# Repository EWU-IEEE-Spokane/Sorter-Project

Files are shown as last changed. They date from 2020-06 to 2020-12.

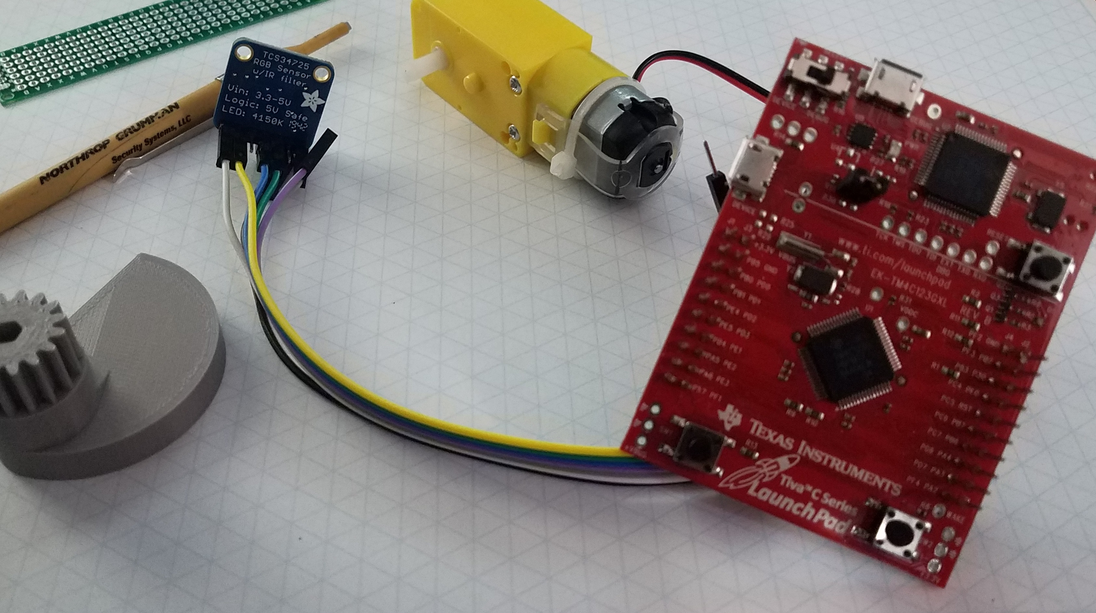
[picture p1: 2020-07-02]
Docs/Mechanical-Engineers/TM4C Color Sensor.jpg

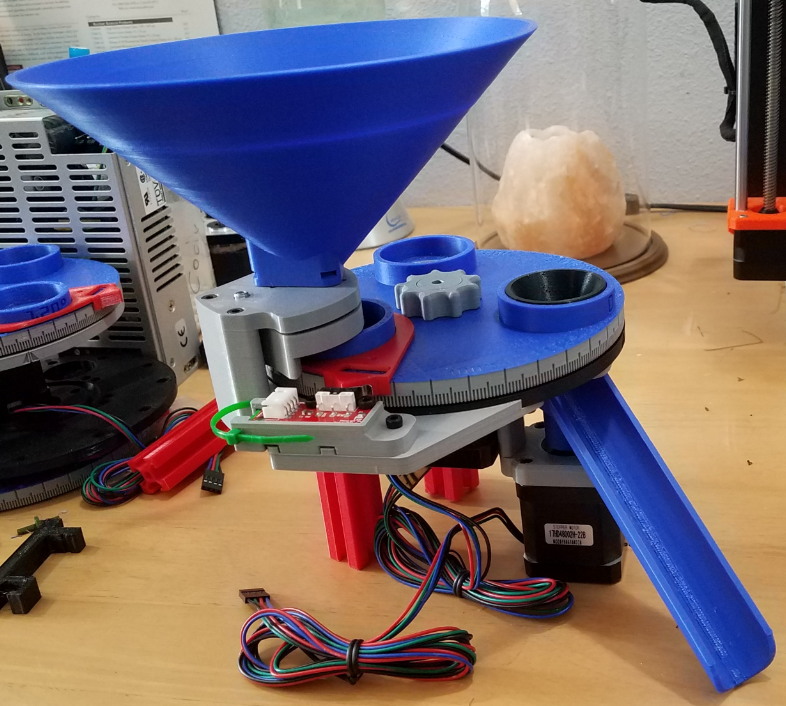
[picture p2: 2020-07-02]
Docs/Mechanical-Engineers/Mechanical Design Printed.PNG

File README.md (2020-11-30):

# Sorter-Project
This is where we host our documentation and code for the Industrial Sorter Project.

# Minutes 11/29/20

We started our meeting looking at the data sheet for the cameras we will be using
    - voti.nl/docs/OV7670.pdf
We also discussed ways to reduce glare in the sorter cups
    - Using a cloth like felt to absorb light
    - Doing the filtering entirely with the image processing algorithm
We talked about ways of getting camera data from the microcontroller to a visible photo
    - Exporting data through UART into a text file, and parsing with some programming language

# Minutes 11/22/20

- We discussed the 3D printed figures from the TinkerCAD fiesta on Friday
    - The printing is going well, other than some more difficult organic shapes

- We discussed methods of holding hand sanitizer
    - Using some kind of sealant on the inside of a 3D printed enclosure
    - Designing parts to screw onto a standard bottle size
    - Using a bag on the inside of the enclosure
    - Partnering with the chemistry department for the solution
    - Solving the problem of viscosity to keep the dispensing speed reasonable
    - Nhat has a working prototype
    - Working on the software side of things

- We revisited the sorter machine design document
    - We accomplished a lot of what we set out to do
    - Some things we descoped, or determined weren't necessary

- We discussed Git and GitHub
    - Over winter break, we may do a workshop
    - Mathew has uploaded his code to GitHub

- We talked about cameras for the image processing
    - Here is a link to the camera we're considering:
        https://www.amazon.com/HiLetgo-OV7670-640x480-0-3Mega-Arduino/dp/B07S66Y3ZQ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

# Minutes 11/8/2020

We started the meeting with discussing a presentable document for the image processing algorithm
- Mathew will be working on this

We had a demo by Cody of the Sorter (sort of) sorting
- There are still some bugs to work out, the machine is moving between extremes

We discussed getting the presentation prepared
- Things to show while talking
- Videos and Documents to discuss
- Start with a video
- Each team creates a slide
- Future developments
- Team organization
- Mechanical design
- PCB design
- Controls software

We set up the sorter project presentation event invitation through IEEE vTools
- Register here! https://events.vtools.ieee.org/m/247537 

# Minutes 10/25/2020

We started our meeting this week with a presentation from Matt on the image processing
- He successfully coded a working algorithm in Matlab
- Next steps are to get some pictures of skittles that will reflect the final output to test the algorithm, and coding the algorithm in C
- We discussed how the camera interfaces with the Tm4C

Cody is working on the final touches for the mechanical design
- Depending on how complex importing 3D models from 360 to Blender will be, Jaidon will make an animation of the sorter

# Minutes 10/18

Mechanical design
    - Cody has had software issues with Fusion 360, so he is considering buying some aluminum extrusion to finish up

User Interface
    - For the user interface, we are aiming for some status lights
        - Idle, run, pause, stop
    - And 3 buttons
        - Start, pause, and E-stop

Parts Distribution
    - Amy has the funds to send parts out if anyone needs any

Pictures for the Easterner
    - We spent a good amount of the meeting taking some in-meeting pictures for the Easterner to use in the story about our club

Member list
    - We came up with an exhaustive list of club members, and estimated class years for each member

# Minutes from 10/4
We came up with a schedule to prepare for the sorter project presentation on November 18th at 5-6pm. The schedule was posted by Cody, here and on Discord.

We talked about a few ideas for the user interface:
- Using a mini industrial control panel
- Creating a PCB for it
- Attaching LEDs to some type of board

We discussed progress of the image processing:
- Possible use of a raspberry pi
- Issues with tm4c interfacing with camera

Upcoming Events:
- a capture the flag event on Tuesday with Gonzaga, time TBD.
- an educational cyber security event mentioned by Stu (talk to Amy for more info.)
- IEEE day on Tuesday October 6th 11-1pm: come see guest speakers, and participate in a competition of ideas.
- Career center meeting Thursday at 2pm
- A visitor from Easterner magazine is coming to talk during the meeting on Wednesday.

Special thanks to John for signing up to IEEE!

# Minutes from 9/27
We discussed the following miscellaneous:
* Image processing projects, and some examples of OCR with Python were shown by yours truly (Jaidon)
* Possibility of changing meeting times: Friday, or later Tuesday?
* Marketing club meetings and IEEE in classes
* Possibility of PLC projects and remote collaboration on code
* Stu possibly talking about cyber security and iot

We talked a bit about parts distribution:
* Parts list surveys
* Prebuilt kits
* Tm4c and basic parts for all

And the following about the sorter specifically:
* PCB progress (completed and functional)
* Cody will try to benchtest this week
* Cody and Nhat will collaborate on agitator
* 3D printing logistics issues (shipping costs, time)
* Jaidon will package PCBs for shipping
* Ian possibly collaborating with Mathew

Below are upcoming club events:
* Soldering tutorial Wednesday at 6
* EWU IEEE story by Easterner magazine in progress
* SAIL meeting Wednesday

We discussed the following possible new projects:
* Weather station
* Music and sound
* Guitar pedals
* Cyber security
* Halloween project
* Lighting driver

Attendance:
* Jaidon
* Chris
* Cody
* Nhat
* Mathew

Ieee members:
* Jaidon
* Chris
* Cody
* Amy
* Nhat
* Michael

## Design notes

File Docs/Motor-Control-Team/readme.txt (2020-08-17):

This folder is where the motor control team can upload their documentation, such as the weekly progress reports.

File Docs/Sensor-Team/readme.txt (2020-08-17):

This folder is where the sensor team can upload their documentation, such as the weekly progress reports.

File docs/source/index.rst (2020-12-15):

.. Sorter-Project documentation master file, created by
   sphinx-quickstart on Mon Dec 14 19:26:34 2020.
   You can adapt this file completely to your liking, but it should at least
   contain the root `toctree` directive.

Welcome to Sorter-Project's documentation!
==========================================

.. toctree::
   :maxdepth: 2
   :caption: Contents:
   
   Intro <intro>
   Mechanical System <mechanical>
   Stepper Motor Control <stepper>
   I2C Communication <i2c>
   Color Sensor <color_sensor>
   Color Processing <color_processing>

Indices and tables
==================

* :ref:`genindex`
* :ref:`modindex`
* :ref:`search`

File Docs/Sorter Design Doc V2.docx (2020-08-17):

EWU IEEE Industrial Sorter Project

Project Goals:

System Design

- Practice designing and documenting a complex system
- Make a modular system that supports division of labor and future changes

Industrial controls

- Implement machine with distributed controls – coincides with remote learning
- Ability to scale controls to PLC, HMI, CAN (TM4C), etc.
- Power control and safety circuits

Motor Control

- Build software drivers and hardware for brushed motors and steppers
- Learn motor theory, power transistors, positional control

Sensors, Image Processing and Communications

- Develop familiarity with I2C protocol (industry standard)
- Manage and interpret sensor data
- Scale towards Machine Vision system (Image processing in R&D stages, camera will also use I2C)
- Image processing may apply Machine Learning in future versions

Microcontrollers/Embedded Systems

- Register-level coding on ARM microcontroller
- Real time operations and fault handling

Teams:

Motor Control Team: Jaidon, Wilson, Nhat

Team Lead: Jaidon

- Motor Control (Steppers) - Jaidon, Wilson

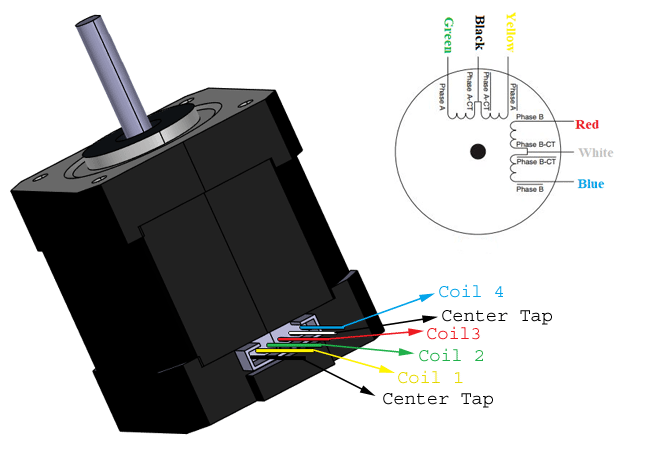
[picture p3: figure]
NEMA 17 Stepper Motor Datasheet, Wiring, Specs & Alternatives

- Agitator Motor – Nhat

Sensor Team: Matt, Amy, Cody, Wilson

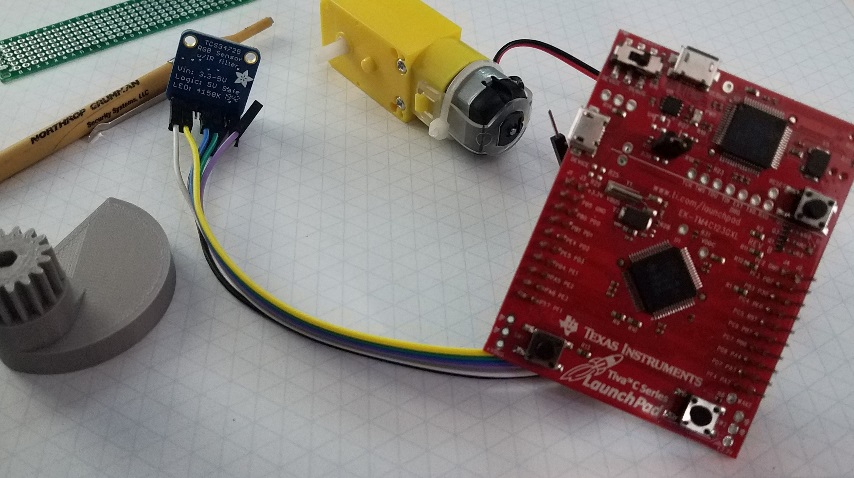
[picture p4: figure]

Team Lead: Cody

- I2C Color Sensor – Amy Swanson, Cody Birkland
- Camera/Image Processing R&D – Matt Sheldon

User Interface Team: Michael, Chris. Nhat

Team Lead:

- LCD R&D Michael
  - 7 segment display for now?

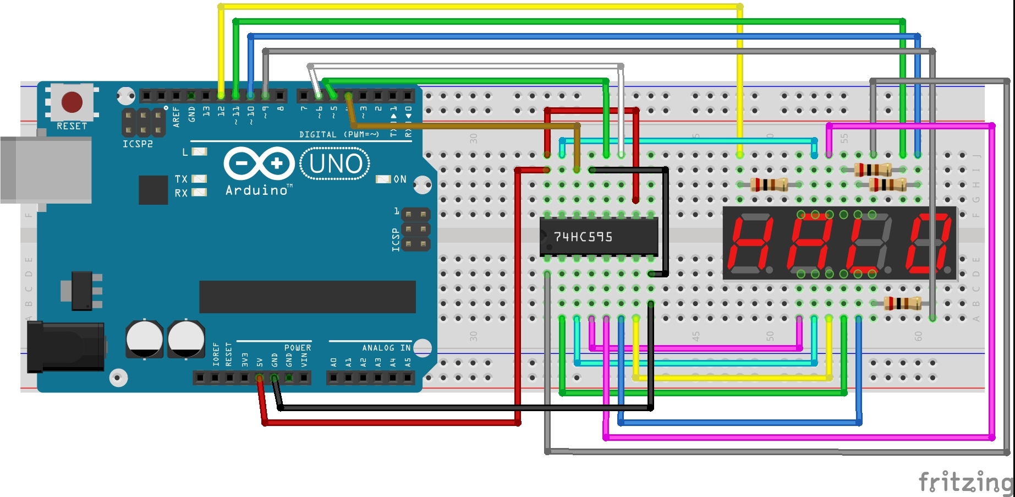
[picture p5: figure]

- Stack Light: Michael

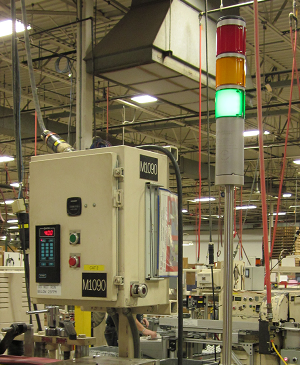
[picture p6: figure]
Stack light - Wikipedia

- Operator Panel – Define switches for control, Define Lights/signals for operation and debug
  - User Interface: Start, Stop (switch), Home (mechanical), E-Stop, Preset (lamp),

Software reset, Debug Mode (switch)

  - Motor Control – “homing” lamp, “ready” lamp
  - Color Sensor – mostly called by software (“sensing color” lamp)
  - Camera calibration when camera is implemented
- RGB LED driver with hex inputs Chris, Michael

System Controls Team: Wilson, Cody

Team Lead: Pending

- Controls Design and Planning
- Mechanical Design – Cody Birkland
- Power System Design (discuss with motor control team)
- Safety Circuits and Controls

Schedule:

Mid-august: Presentable system components

September: Basic working system

~~bench test color sensor to motor interface~~ | | 8/2/2020
Design outline of control systems | | 8/30/2020
finished mechanical prototype | | 8/30/2020
Implement basic user interface | | 9/13/2020
integrate camera and image processing | | 9/27/2020

Next Steps:

- Communicate current system design to user interface team (Cody, Jaidon)
  - Call Diagram
  - Refine Color Sensor code
- Continue mechanical design: chute home switch mount, color sensor mount (Cody)
- Documentation for TM4C programming – setup tutorial (Jaidon: Linux, Amy: Code Composer, Cody/Jaidon: Figure out Visual Studio)
- Prototyping various methods for interfacing: Stack light, UART, 7-segment, etc (User Interface Team)
- Hopper Design and Agitator Motor circuit design (Jaidon and Motor Control Team)
- MISRA C Style Guide PDF £10-20 (Amy talk to Uri) or “ReadTheDocs” designs – discuss in August 4th group meeting
- PLC request from Dr. Walsh (Cody August 3rd)
- Start developing Camera interface (Cody, Matt)

Notes:

Yakindu logic diagram software

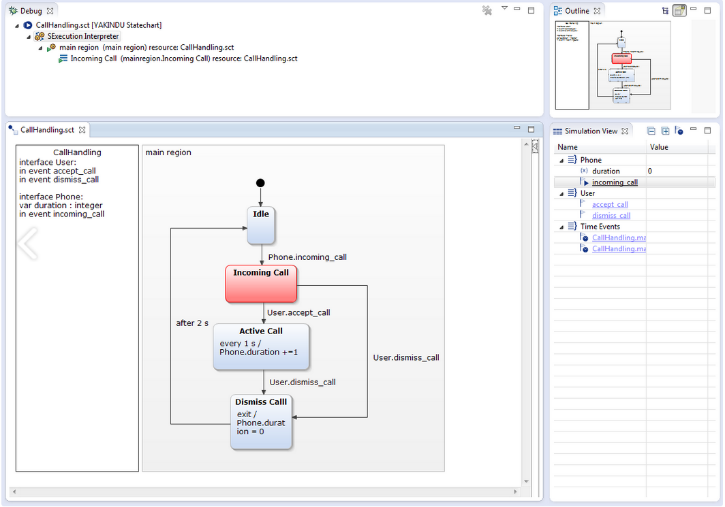
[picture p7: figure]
safety-logic – MoDeS3

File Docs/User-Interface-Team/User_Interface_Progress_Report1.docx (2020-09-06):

Sorter User Interface, Report #1

Goals:

The initial goals for setting up the user interface are to be able to use 4 inputs (Reset, interrupt, Button1, Button2) to move to between 4 simple states that are represented by different LED outputs (Yellow, Red, Green Blue).

What we have done so far:

We have decided on the basic inputs and outputs and how they connect to the user and the LEDs. (See images below)

Worked on getting everyone setup on interfacing with the TM4C.

Gathered all the components we need to prototype the user interface. Put together non-functioning code.

Problems we have had:

Getting everyone setup up to work with the TM4C has been difficult (software to download, compiler errors, etc.).

Limiting the number of inputs to not take up too many pins on the TM4C.

Not knowing what inputs and states we need to implement from other sections of the sorter project.

Actions going forward:

Need to get everybody able to complete the steps necessary to operate the TM4C so we can focus on the fun stuff for the project.

Communicate with the other teams so that we can collaborate more effectively to define the desired inputs, outputs and functionality.

Figure out why the code that we have so far is not operating the way that we would like. Learn how to use the debugger. What is the difference between the device port and the debugger port?

Get all the components connected correctly on the breadboard.

Simple State Diagram

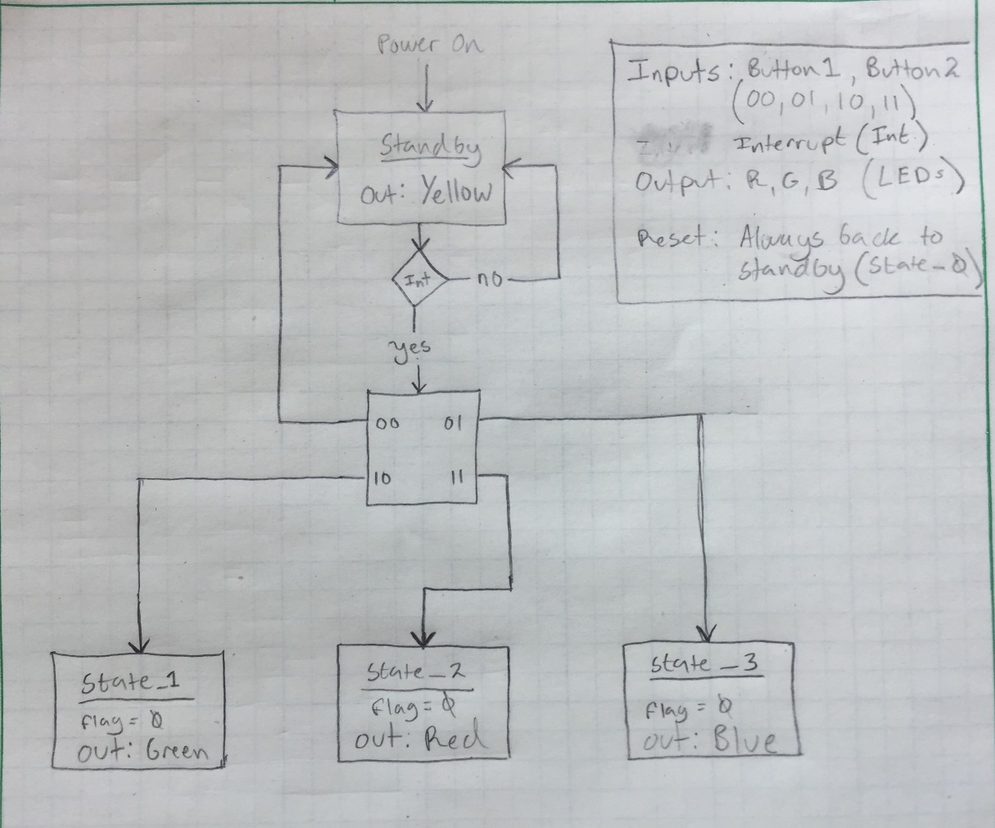
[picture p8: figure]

Input Diagram

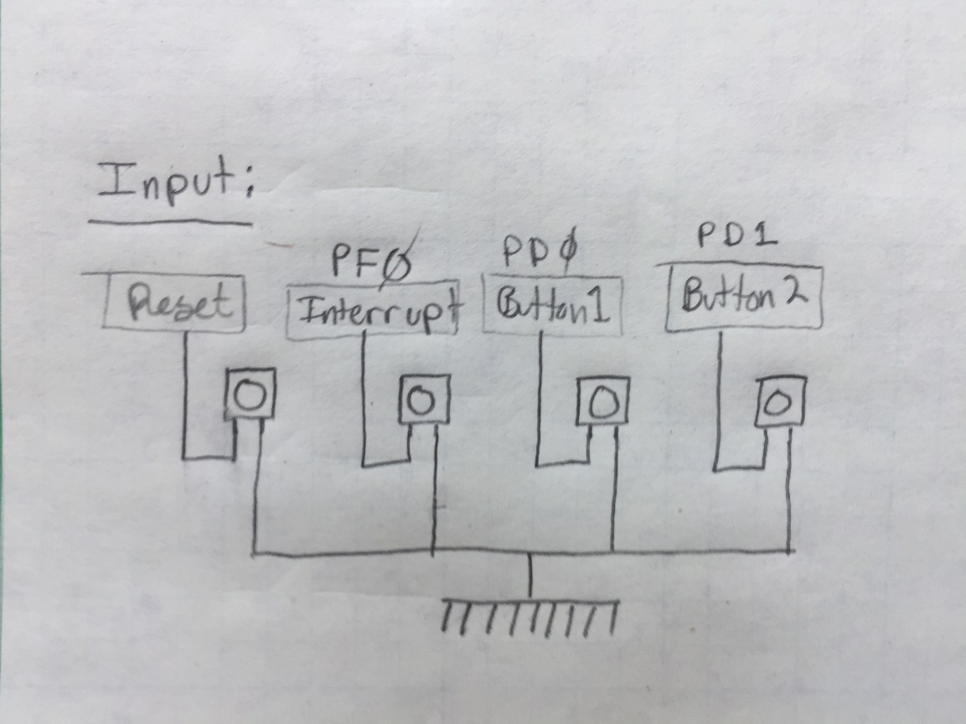
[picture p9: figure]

Output Diagram

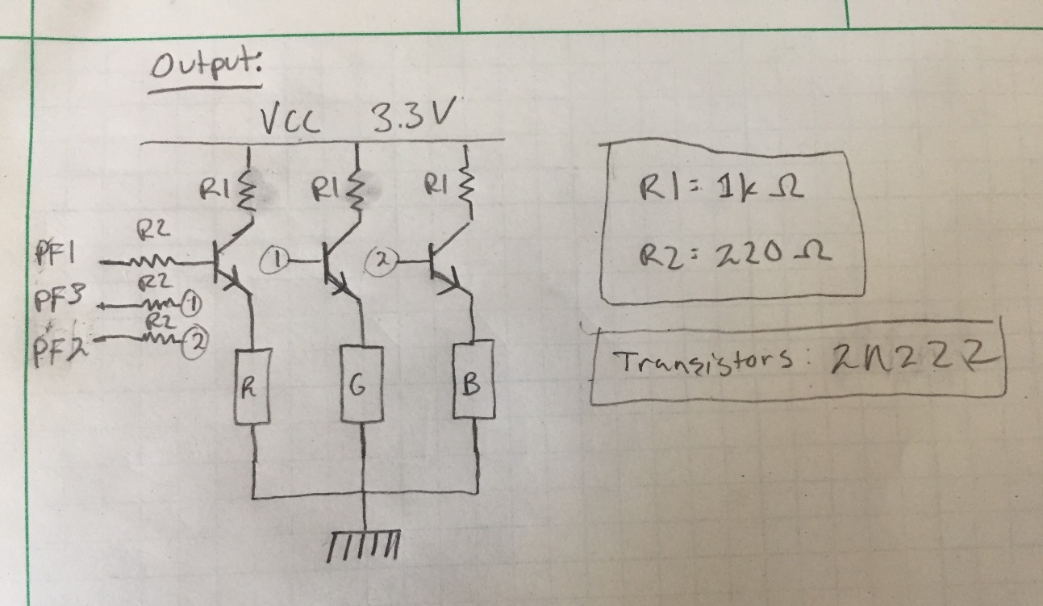
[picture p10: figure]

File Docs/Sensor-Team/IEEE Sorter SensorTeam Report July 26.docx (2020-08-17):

EWU IEEE

Project Weekly Progress Report

Team: Sensors Team

Project: Industrial Sorter

Date: 7/26/2020

What we planned to do last week (copy/paste/summarize previous week)

Last week we planned to continue research into RGB hex color value conversion and gamma correction for the 16-bit color values returned by the color sensor.

We planned a meeting on Saturday in order to catch everyone up on the development of the color sensor code.

Supporting Documentation (website links, GitHub link, pictures)

Basic I2C/Color Sensor Code (initial version that simply obtains 16-bit color values from the sensor): https://github.com/EWU-IEEE-Spokane/TM4C-I2C

UART Output:

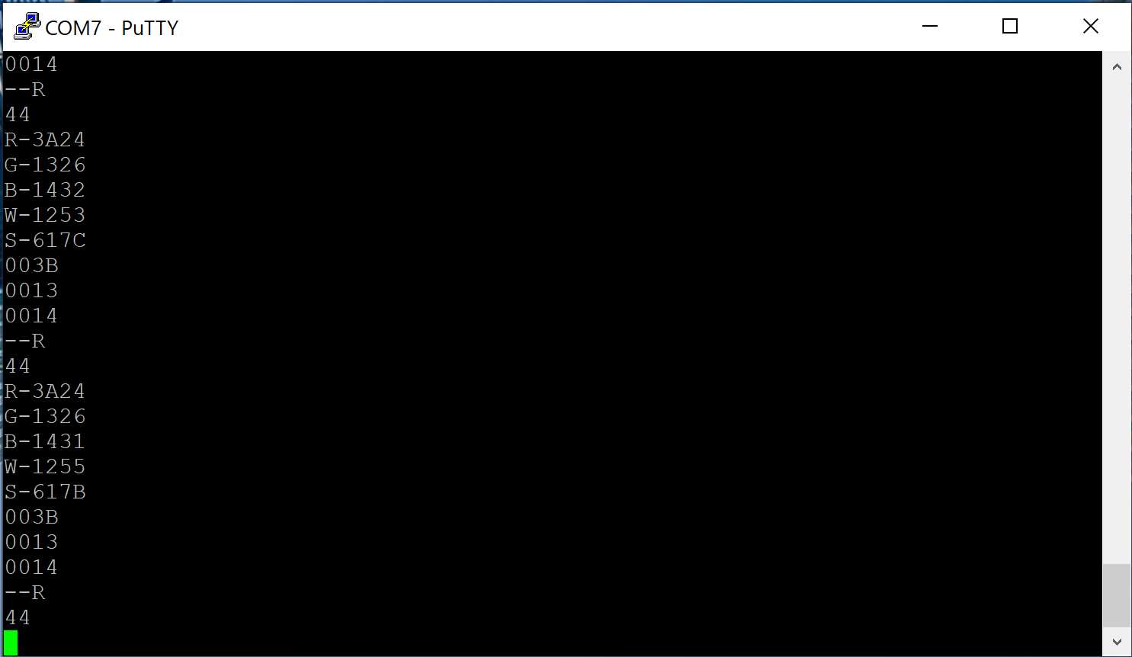
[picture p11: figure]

What we did last week

time spent total: 7 hours

Research:

- Looked into issues with portability of the I2C code. Amy could not compile the code on a Mac, as the compiler had issues on every for loop. Attempted to eliminate initialization within a for loop, but that did not help.

Software:

- Developed sensor code to remove attempts at gamma correction and dynamic compression.
- Added initial attempts to compare color values in their original 16-bit format.

Hardware:

- Built a testing platform for the color sensor that more closely matches the planned end product (enclosed small black tube with colored objects placed at bottom). Before the development work is finalized the CAD models will be developed for the sensor mount and transport cup to enable real-condition testing.

What it accomplished

- We now are ready to develop actual color binning. Being able to sort objects by color will be the majority of the work needed to command the Motor Controller to move based on sorting results.

Why we were unable to accomplish weekly plan if so

- We had to descope in order to make the coming deadline for sensor/motor integration. It is not necessary to implement hex conversion and gamma correction in order to meet this goal. Our time is better spent getting the necessities done.
- We were unable to get the code running on Amy’s machine, so everyone is not caught up on the development. This should be ok as the plan for continued development is linear so it may be best for one person to finish up these items.
- Had issues with compression/gamma correction. Color correction was not working, and results from sensor were definitely digitally saturated (bit overflow). It is possible that analog saturation is causing the sensor to have an incorrect response to color values, where everything is seen as red. Corrections were started by reducing the gain of the sensor from 60x to 4x. Continued analysis is needed.

What we plan to do this week

- Amy will work on parting over the UART code from GitHub in order to gain some insight into why she is having compilation issues. This will also give her a chance to gain familiarity with C for microcontrollers since most of her experience is with assembly language. She’ll also start documenting the setup of Code Composer for the TM4C.
- Cody will develop code that processes the sensor color values into sortation results. The first step will be to resolve the saturation issues so that the sensor returns meaningful values. This may involve tuning of the gain and the integration time of the sensor. It may also be necessary to setup a PWM channel to dim the sensor’s LED.
- Matt will continue camera R&D as time allows, so that there is some refined code ready to be adapted to the camera interface once that is built.
- We need to start communication with the Motion Control Team in order to outline the communication channel between the sensor board and the UMC. We will build a basic interface that drives signals to the motor controller by the end of this week.

How this fits with the overall task/timeline

- We plan to bench test the sensor to motor interface by the end of this week. Getting the sensor to output meaningful color values, then performing a logical sort based on those values will be the majority of what needs to be done on the Sensor Team side of this goal. Adding the motor interface will be more straightforward, though it is dependent on the progress of the Motion Control Team. We will communicate with them in this week’s sorter meeting.
- In order to get meaningful test results from the motor to sensor bench test this week, it may be necessary for the Sensor Team to further descope their design to cut out the incomplete color sorting code. Simply setting up the communication channel and verifying that a list of predetermined sort results can control the motor will give both teams confidence moving forward that they are on the right track. In this case the Sensor Team can add the sorting logic retroactively on top of the tested communication channel.

Why is this important for the project

- Getting this work done will be a major milestone for the project. We will have electronics that will be able to sort objects by color, a communication channel that enables those logical sort results to be passed as control signals to a motor controller, and a motor controller that is able to perform physical sorting.

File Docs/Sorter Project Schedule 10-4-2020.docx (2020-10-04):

Sorter Project Presentation: Wednesday, November 18th at 5-6 PM

Weeks starting Sunday

10-4: Finish Frame design and manufacturing, Agitator mechanical design, Driver design discussion. Continue Image processing

10-11: Full system test with finished mechanical design, implement agitator

10-18: Bug fixes, Cable management, start distributing parts

10-25: Finalize User interface, beautify. Evaluate image processing technology readiness

11-1: Start generating presentation materials (slide show, documentation, video?)

11-8: finish presentation, dress rehearsal

11-15: week of presentation

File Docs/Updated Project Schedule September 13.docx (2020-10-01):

Sorter Project Revised Schedule 9-13-2020

Sept 13 – Attempted complete system prototype initial test:

- Had issues with underpowered 5V power supply (max output 700mA).
- May want to isolate 5V logic rail and 5V motor power
- Need Frame and cable management
- Need to test color sensor performance in actual sorter conditions
- Code had issues with shared global variables for the chute and turntable motors

Sept 20 – Have frame designed, acquire suitable 5V supply, continue user interface design, test improved code, test color sensor performance, start power supply isolation circuit design, test breadboarded prototype

Sept 23 – quarter starts

Sept 27 – Have PCB assembled, attempt another complete system test, start mass producing components, generate BOM and assembly instructions

Oct 4 – have kits shipped out, start integrating user interface

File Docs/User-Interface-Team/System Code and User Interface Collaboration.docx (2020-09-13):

System Code and User Interface Collaboration

EWU IEEE Industrial Sorter Project

September 6, 2020

System code is shown in bold

User interface code wishlist is shown as highlighted

From “Sorter.c”:

Main{

Configure()

ShowReadyLight() //right now the code blinks 3 times to show configure worked

While(presetButtonNotPushed){} //wait until operator hits preset

While(preset){

homeTable()

homeChute()

while(runButtonNotPushed){} //wait here until operator hits start

while(run){

singleSort() //rotate turntable to get product in front of sensor and drop previous into chute

//call sensor code to get sort result integer: 0=reject, 1-5=skittle colors

//move chute to correct cup

if(estop){

preset = FASLE;

run = FALSE;

//break out of loops, but power to motors has been cut so system is safe

}

if(softStop){

run = FALSE;

}

}

}

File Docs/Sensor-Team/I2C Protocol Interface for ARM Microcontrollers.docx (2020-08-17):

I2C Protocol Interface for ARM Microcontrollers

Industrial Sorter Project

Cody Birkland, EWU IEEE Student Chapter

August 16, 2020

Problem:

We need to interface with the color sensor for the first-stage development of the Sorter Project. The TCS34725 Color Sensor uses the I2C protocol for control signals and data, and the TM4C has multiple integrated I2C controllers. We need to understand the details of the protocol such as the signal characteristics, symbol meanings, and other information specific to the color sensor and the microcontroller.

Research:

The details of the I2C Protocol were researched online. The reference used are:

- I2C Basics: https://www.allaboutcircuits.com/technical-articles/introduction-to-the-i2c-bus/
- I2C DigiKey article: https://www.digikey.com/en/articles/why-the-inter-integrated-circuit-bus-makes-connecting-ics-so-easy
- More reading and address list: https://learn.adafruit.com/i2c-addresses
- TCS34725 Datasheet: https://github.com/EWU-IEEE-Spokane/Sorter-Project/blob/master/I2C%20Color%20Sensor/TCS34725%20Datasheet.pdf
- Reference to TM4C Datasheet https://github.com/EWU-IEEE-Spokane/TM4C-Resources/blob/master/TM4C%20Datasheet.pdf - pages:
    - Introduction – Page 997
    - Block diagrams – Page 1008
    - Initialization Procedure – Page 1015
- Info on SCCB (I2C for cameras): http://forums.parallax.com/uploads/attachments/49380/88241.pdf

The protocol is summarized here:

- I2C utilizes a simple 2-wire communication channel consisting of a Serial Clock wire (SCL) and a Serial Data wire (SDA). Both signals are connected to the positive supply voltage via pull up resistors.
- Communications occur between a Master Device which controls the bus and one or more Slave Devices that can send and receive data when commanded to. There are provisions for having Multiple Masters in one bus, but this is not common in basic applications.
- Data is sent one byte (8 bits) at a time in a Transmission Session. A transmission starts with a start signal, then is immediately followed by the 7-bit Address of the Slave Device to be communicated with. This is then followed by a single bit that specifies Read or Write. This determines if the next 8 bits are data Written to the Slave Device, or 8 bits of data Read from the Slave Device. Following the data, the receiving device asserts a single bit Acknowledge (ACK) signal that tells the transmitting device that the data was successfully received. With a valid ACK, the transmitting device can send as many successive bytes of data as necessary, each with their own ACK bit that must be valid. Once the data is sent, the Master Device asserts a Stop signal that terminates the Transmission Session.

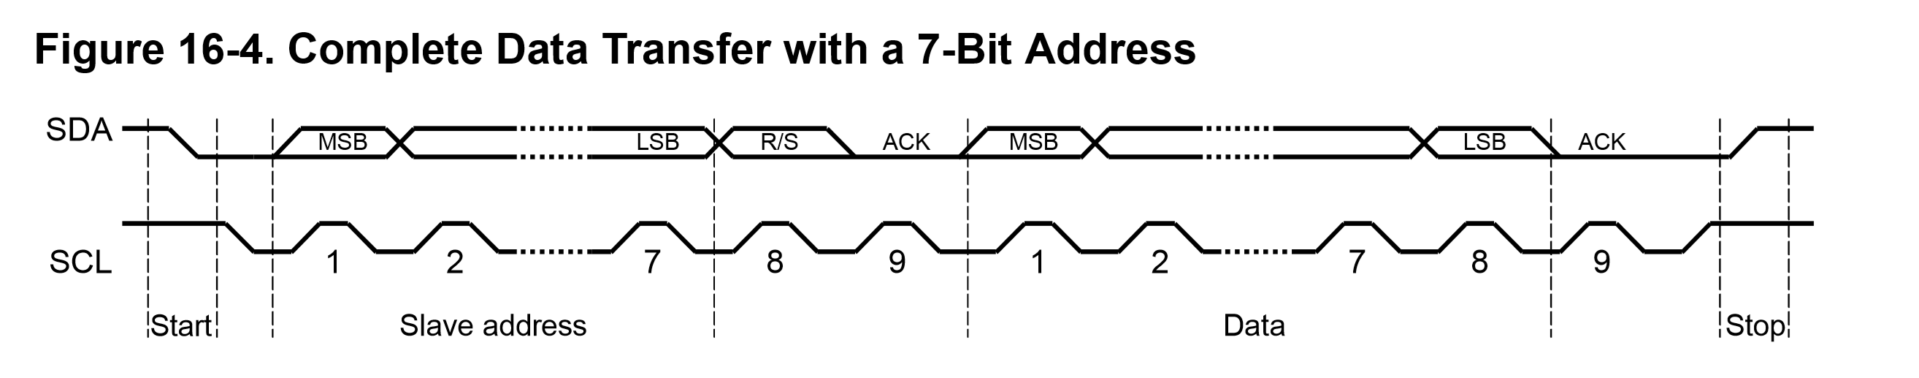
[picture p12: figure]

- Communications can occur in Two modes: A Single Start mode, where an initial Start, Address, and Read/Write command is followed by one or more bytes of data. In this mode, all data in the Transmission is either Read from or Written to the Slave Device. There is also a Repeated Start mode, where multiple Start signals can be used to switch between Read and Write modes without stopping the Transmission.

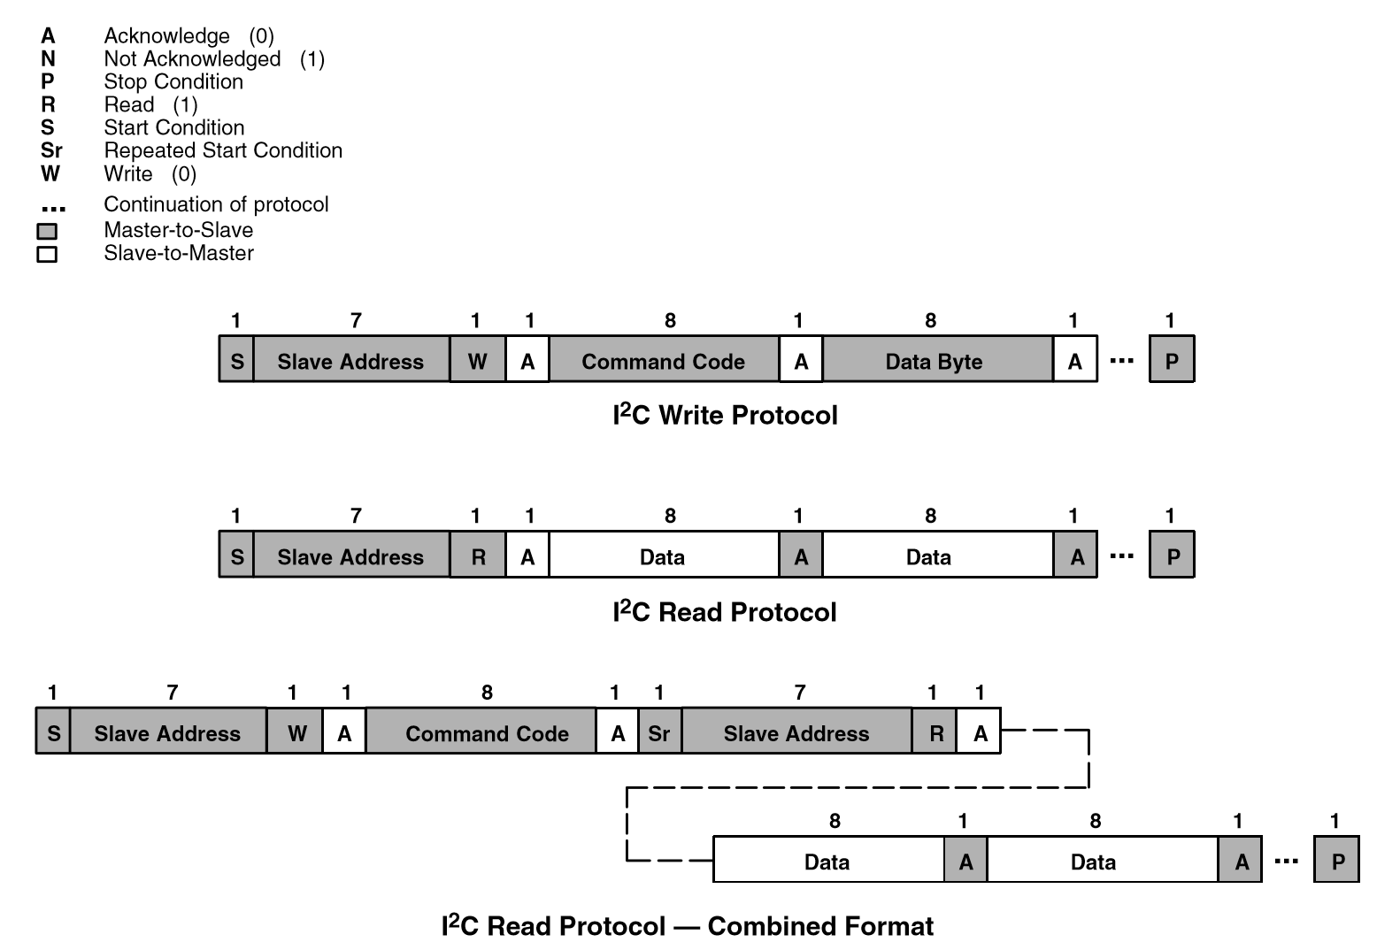
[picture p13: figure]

- There are 4 legal symbols: Start, Data High, Data Low, Stop
- START: Clock high, Data transitions from high to low
- STOP: Clock high, Data transitions from low to high
- Data is either low or high. It is read whenever the clock is high. The data is only permitted to change when the clock is low.
- The ACK signal is the bit immediately following the Data byte, and is low for a successful Acknowledge. This bit behaves the same as a Data bit.

Action:

After learning the intricacies of the protocol, the TM4C Datasheet was used as a guide to develop C code to initialize an I2C module on the Microcontroller then establish a working communication channel with the TCS34725 Color Sensor. After significant debugging, the code was developed to enable reliable communications with the sensor in Single Start mode only.

Initial Code: https://github.com/EWU-IEEE-Spokane/TM4C-I2C

For reasons that have yet to be fully understood, the code implementing a Multiple Start mode driver was not operational and would fail to change the mode of operation. The code also lacks failure handling and an intelligent bus monitoring function. For now, there are significant delays to allow ample time for the communications to complete before moving on. This will need to be optimized in the future.

Value:

Having a working interface for the Color Sensor allows us to move forward with the development of the sensor aspect of the project. This is a vital part of the sorter machine and getting the sensor code working is a major milestone. Additionally, developing an understanding of the I2C protocol will be useful for interfacing with the camera as development continues, since the SCCB protocol that it uses is closely related to I2C.

Beyond this project, the framework for a general-purpose I2C driver for the TM4C will give us a major start towards working with a multitude of different devices. I2C is such a popular communication protocol that there are thousands of devices that use it out there, covering almost everything imaginable such as external memory, accelerometers, and display devices. Before pursuing the many applications out there, we should refine the code to be general purpose, fault tolerant, efficient, and supportive of the Multiple Start mode.

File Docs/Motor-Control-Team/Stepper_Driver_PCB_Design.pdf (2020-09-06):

# Stepper Driver PCB Design

# Skittle Sorter Project Jaidon Lybbert, Motor Control Design Lead, EWU IEEE Student Chapter

08/23/20

This document describes the current stepper motor driver PCB design.

# 3D View:

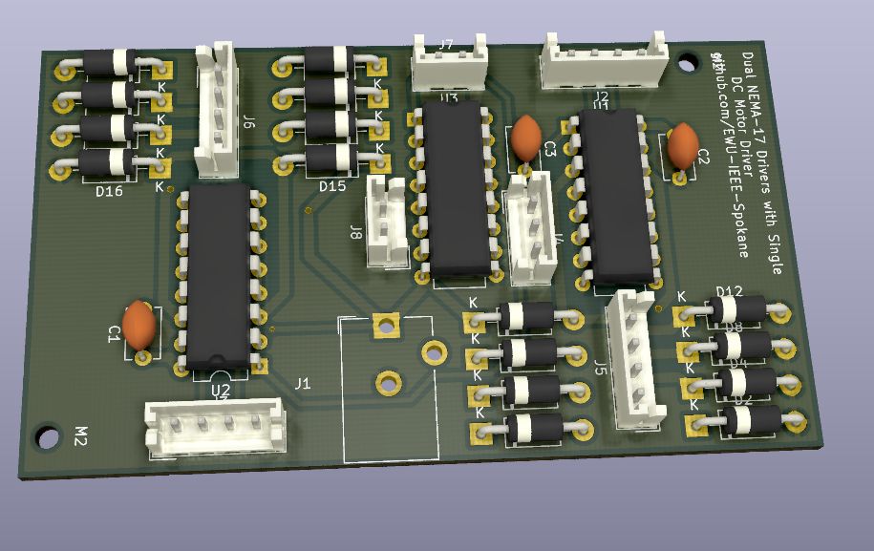
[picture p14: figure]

Fig. 1: Current version of the driver PCB. The outer ICs are l293B chips, and the center IC is an l293D chip. The l293Bs have 2 external 1N4001 flyback diodes for each of their 4 output pins (J5, J6). The connectors at the top end of each IC are the logical inputs (J2, J7, J3) and

# connector J4 has one active high enable pin for each IC. Each IC has one 0.22uF bypass

capacitor for its logic power supply input.

# PCB Specifications: - Layers: 2 - Dimensions: 44.45 x 76.20mm - Thickness: 1.6mm

- Copper weight: 2 Oz.

# Components List:

"Source:" | "C:\Users\Jaidon Lybbert\Documents\Classwork\EENG250\Lab0\MotorDriver\Motor_Driver\Motor_Driver.sch"
"Date:" | "8/23/20 2:54:10 PM"
"Tool:" | "Eeschema (5.1.5-108-gad11b7ebd)-1"
"Component Count:" | "30"
"Ref" | "Value" | "Part" | "Footprint" | "Description" "Vendor"
"C1" | "0.22uF" | "Device:C_Small" | "Capacitor_THT:C_Disc_D5.1mm_W3.2mm_P5.00mm" | "Unpolarized capacitor, small symbol" ""
"C2" | "0.22uF" | "Device:C_Small" | "Capacitor_THT:C_Disc_D5.1mm_W3.2mm_P5.00mm" | "Unpolarized capacitor, small symbol" ""
"C3" | "0.22uF" | "Device:C_Small" | "Capacitor_THT:C_Disc_D5.1mm_W3.2mm_P5.00mm" | "Unpolarized capacitor, small symbol" ""
"D1" | "1N4001" | "Diode:1N4001" | "Diode_THT:D_DO-41_SOD81_P10.16mm_Horizontal" | "50V 1A General Purpose Rectifier Diode, DO-41"
"D2" | "1N4001" | "Diode:1N4001" | "Diode_THT:D_DO-41_SOD81_P10.16mm_Horizontal" | "50V 1A General Purpose Rectifier Diode, DO-41"
"D3" | "1N4001" | "Diode:1N4001" | "Diode_THT:D_DO-41_SOD81_P10.16mm_Horizontal" | "50V 1A General Purpose Rectifier Diode, DO-41"
"D4" | "1N4001" | "Diode:1N4001" | "Diode_THT:D_DO-41_SOD81_P10.16mm_Horizontal" | "50V 1A General Purpose Rectifier Diode, DO-41"
"D5" | "1N4001" | "Diode:1N4001" | "Diode_THT:D_DO-41_SOD81_P10.16mm_Horizontal" | "50V 1A General Purpose Rectifier Diode, DO-41"
"D6" | "1N4001" | "Diode:1N4001" | "Diode_THT:D_DO-41_SOD81_P10.16mm_Horizontal" | "50V 1A General Purpose Rectifier Diode, DO-41"
"D7" | "1N4001" | "Diode:1N4001" | "Diode_THT:D_DO-41_SOD81_P10.16mm_Horizontal" | "50V 1A General Purpose Rectifier Diode, DO-41"
"D8" | "1N4001" | "Diode:1N4001" | "Diode_THT:D_DO-41_SOD81_P10.16mm_Horizontal" | "50V 1A General Purpose Rectifier Diode, DO-41"
"D9" | "1N4001" | "Diode:1N4001" | "Diode_THT:D_DO-41_SOD81_P10.16mm_Horizontal" | "50V 1A General Purpose Rectifier Diode, DO-41"
"D10" | "1N4001" | "Diode:1N4001" | "Diode_THT:D_DO-41_SOD81_P10.16mm_Horizontal" | "50V 1A General Purpose Rectifier Diode, DO-41"
"D11" | "1N4001" | "Diode:1N4001" | "Diode_THT:D_DO-41_SOD81_P10.16mm_Horizontal" | "50V 1A General Purpose Rectifier Diode, DO-41"
"D12" | "1N4001" | "Diode:1N4001" | "Diode_THT:D_DO-41_SOD81_P10.16mm_Horizontal" | "50V 1A General Purpose Rectifier Diode, DO-41"
"D13" | "1N4001" | "Diode:1N4001" | "Diode_THT:D_DO-41_SOD81_P10.16mm_Horizontal" | "50V 1A General Purpose Rectifier Diode, DO-41"
"D14" | "1N4001" | "Diode:1N4001" | "Diode_THT:D_DO-41_SOD81_P10.16mm_Horizontal" | "50V 1A General Purpose Rectifier Diode, DO-41"
"D15" | "1N4001" | "Diode:1N4001" | "Diode_THT:D_DO-41_SOD81_P10.16mm_Horizontal" | "50V 1A General Purpose Rectifier Diode, DO-41"
"D16" | "1N4001" | "Diode:1N4001" | "Diode_THT:D_DO-41_SOD81_P10.16mm_Horizontal" | "50V 1A General Purpose Rectifier Diode, DO-41"
"J1" | "Barrel_Jack""Connector:Barrel_Jack" "Connector_BarrelJack:BarrelJack_Horizontal" | "DC Barrel Jack" | ""
"J2" | "Conn_01x04_Female" | "Connector:Conn_01x04_Female" | "Connector_JST:JST_EH_B4B-EH-A_1x04_P2.50mm_Vertical"
"J3" | "Conn_01x04_Female" | "Connector:Conn_01x04_Female" | "Connector_JST:JST_EH_B4B-EH-A_1x04_P2.50mm_Vertical"
"J4" | "Conn_01x03_Female" | "Connector:Conn_01x03_Female" | "Connector_JST:JST_EH_B3B-EH-A_1x03_P2.50mm_Vertical"
"J5" | "Conn_01x04_Male" | "Connector:Conn_01x04_Male" | "Connector_JST:JST_EH_B4B-EH-A_1x04_P2.50mm_Vertical"
"J6" | "Conn_01x04_Male" | "Connector:Conn_01x04_Male" | "Connector_JST:JST_EH_B4B-EH-A_1x04_P2.50mm_Vertical"
"J7" | "Conn_01x02_Female" | "Connector:Conn_01x02_Female" | "Connector_JST:JST_EH_B2B-EH-A_1x02_P2.50mm_Vertical"
"J8" | "Conn_01x02_Male" | "Connector:Conn_01x02_Male" | "Connector_JST:JST_EH_B2B-EH-A_1x02_P2.50mm_Vertical"
"U1" | "L293B" | "Driver_Motor:L293" | "Package_DIP:DIP-16_W7.62mm" | "Quadruple Half-H Drivers"""
"U2" | "L293B" | "Driver_Motor:L293" | "Package_DIP:DIP-16_W7.62mm" | "Quadruple Half-H Drivers"""
"U3" | "L293D" | "Driver_Motor:L293D" | "Package_DIP:DIP-16_W7.62mm" | "Quadruple Half-H Drivers"""

# Additional notes: - The l293B chips require heatsinks

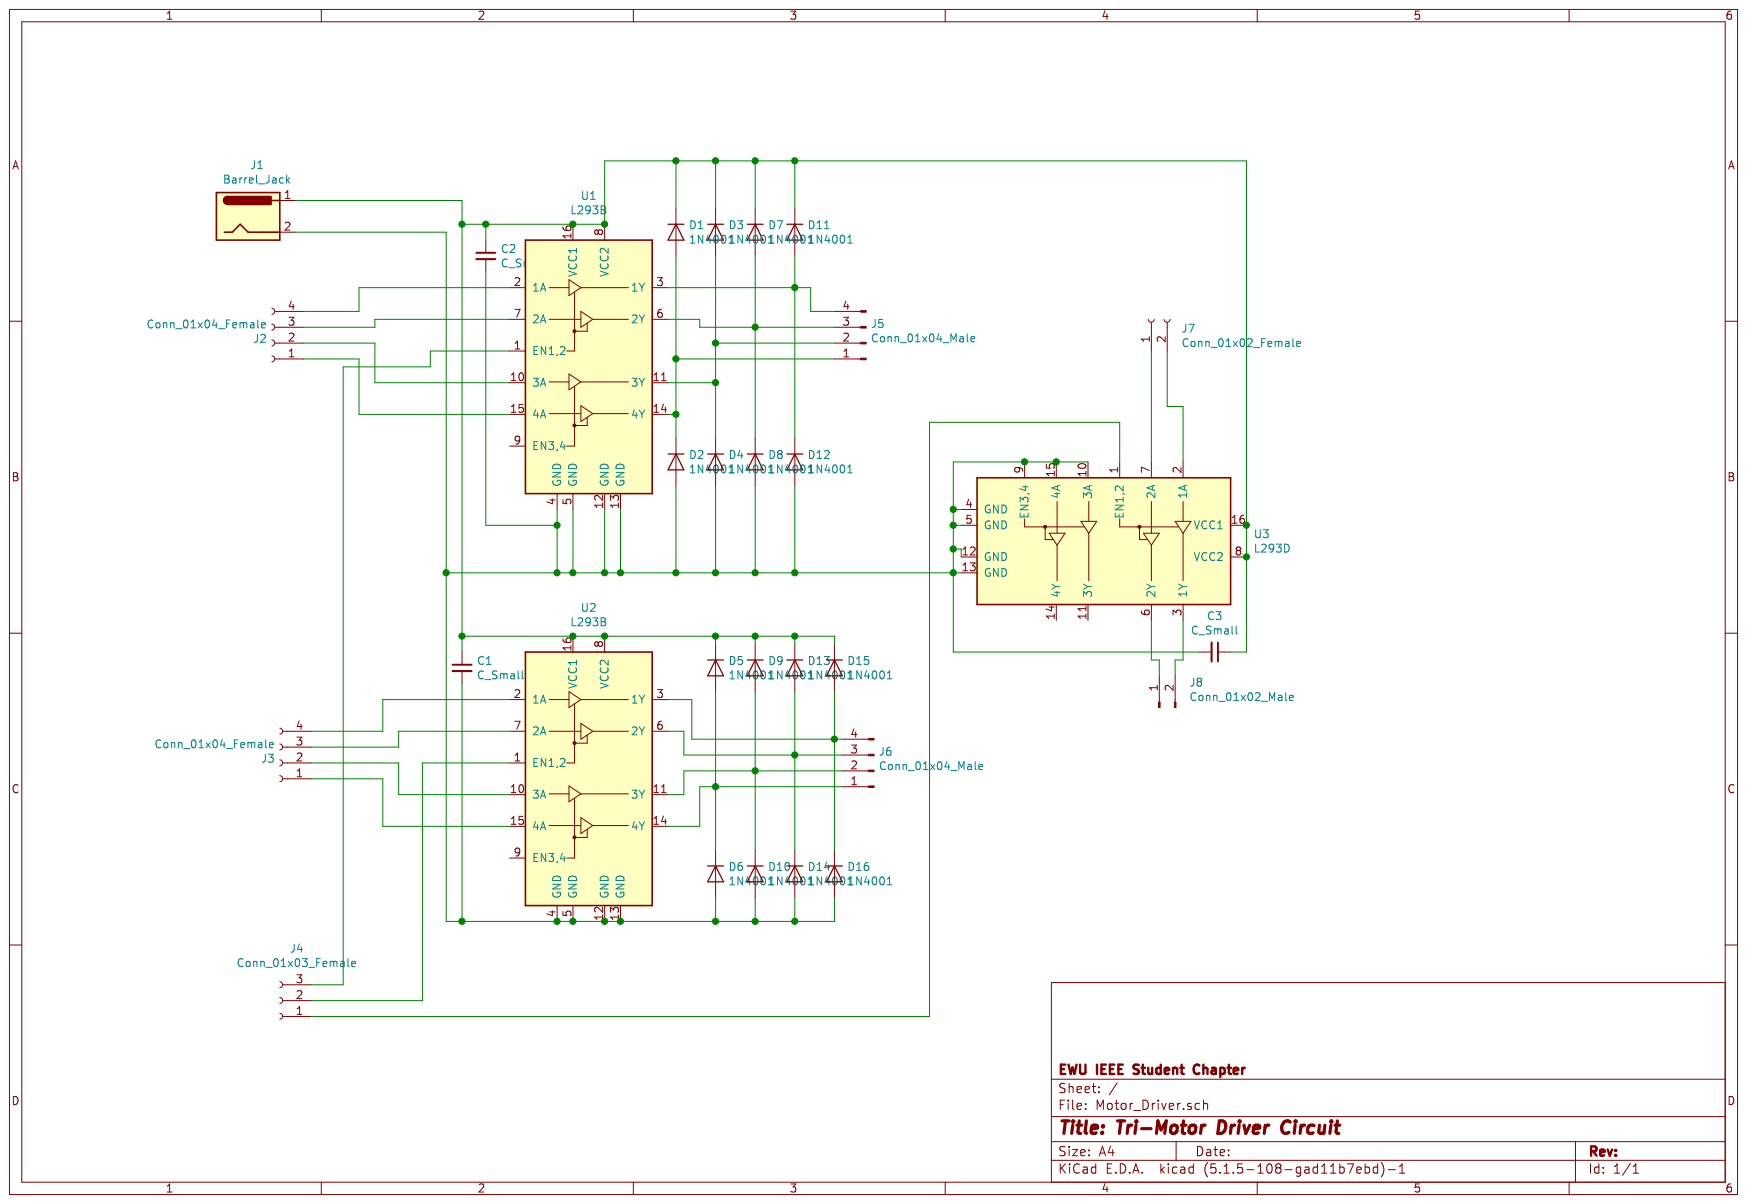
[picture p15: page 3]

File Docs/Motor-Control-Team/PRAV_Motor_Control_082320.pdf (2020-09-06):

### Motor Control Progress Report #8

Skittle Sorter Project
Jaidon Lybbert, Motor Control Design Lead, EWU IEEE Student Chapter
Week of 08/23/20

Problem:
- The PCB design for the motor driver circuit was missing current limiting resistors on the l293B outputs
- A team member (Wilson) was interested in the motor control development, but needed assistance catching up to the current state of the project

Research:
- A 2W 2 Ohm resistor was found, and the dimensions were used to choose the correct footprints

Action:
- The PCB design was modified to accommodate the new components
- A meeting was made with Wilson, in which we were able to get his sorter prototype working with the latest code

Value:
- With the new additions, the PCB design is ready to be sent off for manufacturing
- Bringing additional team members up to date will allow for concurrent development

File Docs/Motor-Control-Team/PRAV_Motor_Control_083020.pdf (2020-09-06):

### Motor Control Progress Report #9

Skittle Sorter Project
Jaidon Lybbert, Motor Control Design Lead, EWU IEEE Student Chapter Week of 08/30/20

Problem:
- The completed PCB design had not been reviewed and sent off for manufacturing
- No progress with implementing ReadTheDocs had been made
- System timing uses busy wait loops and is not tied to any real time
- Wilson needed additional help getting caught up with code development

Research:
- Usage of the SysTick peripheral on the tm4c from the datasheet
- Implementation of ReadTheDocs with github
- https://docs.readthedocs.io/en/stable/intro/getting-started-with-sphinx.html
- Sphinx
- https://docs.readthedocs.io/en/stable/intro/getting-started-with-sphinx.html
- https://www.sphinx-doc.org/en/master/
- reStructuredText
- https://www.sphinx-doc.org/en/master/usage/restructuredtext/basics.html

Action:
- Sent PCB design to JCLPCB for manufacturing
- Implemented ReadTheDocs for a private repository as practice
- Modified sorter.c and stepper.c functions to use real times, by adopting existing code written by Amy Swanson
- A meeting was made with Wilson, in which we went over the stepper code implementation, and he was able to build the project with make

Value:
- Everything is done with the PCBs until they get delivered
- ReadTheDocs will allow us to create user friendly documentation of our code
- System timing is now predictable and precise

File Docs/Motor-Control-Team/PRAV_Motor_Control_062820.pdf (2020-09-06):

### Motor Control Progress Report #2

Skittle Sorter Project
Jaidon Lybbert, Motor Control Design Lead, EWU IEEE Student Chapter
Week of 06/28/20

Problem:
- With the limitations of being a remote organization, and much of our work being done in software, we need a way to collaborate effectively and in an organized manner
- With separate teams working on different systems, it is necessary to communicate our designs to one another to fit them together and avoid conflicts

Research:
- While organizing my section of the newly formed GitHub page, I researched the formatting of a .gitignore file to exclude object files and other unnecessary files from being pushed to the repository and cluttering the filesystem.
- https://git-scm.com/docs/gitignore

Action:
- Created a design document for the universal motor controller (UMC) including inputs and outputs to act as a reference material for myself and other teams
- Created a development document to communicate my progress
- Uploaded current code to GitHub, and organized folders
- The following commits were made:
- Created design document for UMC
- Uploaded project code to GitHub
- Added development document
- Organized and configured .gitignore

Value:
- Using team-oriented development tools encourages others to do the same, and fosters consistent progress and activity within the organization
- Creating design documentation allows others to interface with your section of the project easily
- Communicating progress, and maintaining a history, lowers the barrier of entry for newcomers to the team

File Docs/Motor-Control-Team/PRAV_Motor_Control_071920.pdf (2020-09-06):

### Motor Control Progress Report #3

Skittle Sorter Project
Jaidon Lybbert, Motor Control Design Lead, EWU IEEE Student Chapter
Week of 07/19/20

Problem:
- As code grows, it is necessary to make adjustments to the structure to make it more maintainable, in this case, my code had outgrown its single stepper.c file, and needed to be split into sections that made sense and were portable
- Development thus far had been using a unipolar 4-phase 28byj-48 stepper motor, which is not the motor used for our project, small modifications to the code had to be made to adapt to the bipolar 2-phase NEMA-17 motor
- The NEMA-17 motor requires a large current, and a beefier driver circuit, for this we decided on the l293B dual H-bridge driver, which would need to be interfaced with the motor

Research:
- Splitting files required some brush up on how to link compiled c object files using make, as well as what should and should not be included in a header file
- https://www.cs.colby.edu/maxwell/courses/tutorials/maketutor/
- https://www.tutorialspoint.com/cprogramming/c_header_files.htm
- Learning about how a bipolar stepper motor is driven compared to a unipolar motor was a necessity. The following document contains very detailed information about different methods of driving stepper motors
- https://www.st.com/resource/en/application_note/cd00003774-stepper-motor-drivi ng-stmicroelectronics.pdf (https://www.st.com/resource/en/application_note/cd00003774-stepper-motor-driving-stmicroelectronics.pdf)
- It was necessary to refer to the L293B datasheet to interface the IC with the motor
- https://www.st.com/resource/en/datasheet/l293b.pdf
- Flyback diodes were used in the driver circuit, and consequently researched
- https://en.wikipedia.org/wiki/Flyback_diode

Action:
- The huge stepper.c file was split into init.c, umc.c, and stepper.c, with associated header files
- The code was modified to add support for driving the NEMA-17 motor
- A “home” switch input was added to an onboard button along with an associated debouncing function
- The driver circuit was built, and interfaced with the tm4c and NEMA-17 for testing

Value:
- Maintaining existing code improves readability and prevents future issues from arising
- Constructing the circuit for the NEMA-17 allows for testing of the software and hardware, as well as further development of functionality
- Basic inputs to the system allows for more robust testing

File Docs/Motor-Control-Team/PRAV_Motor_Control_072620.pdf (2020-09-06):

### Motor Control Progress Report #4

Skittle Sorter Project
Jaidon Lybbert, Motor Control Design Lead, EWU IEEE Student Chapter
Week of 07/26/20

Problem:
- Until now, most of the inputs for testing have been done in software. In order to interface to the rest of the system, hardware inputs must be used
- Through the development process, certain code blocks and parameters to functions have become obsolete
- The motor had not been tested with the color sensor, which is another module with significant progress made, and which functions on its own
- While we originally intended to have the motor control implemented on a separate microcontroller than the rest of the components in the system, it was determined that it would be more reasonable to implement many of the systems on the same board along with the motor controller

Research:
- The I2C protocol was researched for some background knowledge in order to understand the color sensor’s code
- https://learn.sparkfun.com/tutorials/i2c/all

Action:
- Inputs were initialized for the UMC according to the design document
- Unnecessary parameters were removed from code functions
- A central control file “sorter.c” was added to call functions from both motor control and sensor code
- A meeting was made with the sensor team, and the motor control was successfully integrated with the color sensor. We were able to read a color, and the chute correctly moved to the corresponding color’s bin location.
- It was decided that the motor controller would have software inputs as opposed to hardware inputs in order to make the interfacing process easier to implement and maintain, as well as save on components

Value:
- A central control file allows us to keep existing, working code separate from new, rapidly developing code
- Interfacing the two systems opened our eyes to the error in our design approaches, and allowed us to make adjustments accordingly
- Now that the two systems are interfaced and work, we are much closer to a presentable working product

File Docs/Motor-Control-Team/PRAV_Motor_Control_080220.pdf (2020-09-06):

### Motor Control Progress Report #5

Skittle Sorter Project
Jaidon Lybbert, Motor Control Design Lead, EWU IEEE Student Chapter
Week of 08/02/20

Problem:
- Because we decided we are going to interface with the stepper motor control through software rather than hardware, the code has to be modified to take controls as parameters in code, rather than as GPIO inputs. Additionally, since the UMC was intended to be dedicated to a single motor, the code now must be abstracted so that it can be used for several motors.
- The I2C.c code used for the color sensor was large and consisted of several sections (I2C, UART, color processing) that could be separated into individual modules.
- The motor control code had dependencies that were implementation specific (init.c primarily) which prevented the code from being separated and used elsewhere
- The color sensor and motor control worked together, but had bugs
- Issues arose using VSCode to flash binaries to the tm4c when the current flashed program included the color sensor code

Research:
- Research was done on color sensor used in order to integrate the hardware into my home project setup, and further understand the sensor code
- https://www.alldatasheet.com/view_datasheet.jsp?Searchword=TCS34725

Action:
- Abstracted stepper code to be functional with multiple motors driven from the same tm4c
- Helped color sensor team in splitting large I2C.c file into smaller modules
- Removed dependencies and hardcoded addresses from stepper code
- Fixed bugs with integration of the sensor code with the motor driving code

Value:
- With the new code abstractions, we will be able to drive stepper motors for both the chute and the table components of the sorting machine
- By splitting the I2C.c file, we are now able to port the smaller modules into other projects in the future, without including a lot of unnecessary code that would add clutter and confusion
- Removing dependencies and hardcoded addresses from the stepper code prepares us to eventually compile this code as a library object file to be used in projects without the need for recompiling
- Fixing the bugs introduced with the interface of the two systems allows for further testing and integration with the remaining systems

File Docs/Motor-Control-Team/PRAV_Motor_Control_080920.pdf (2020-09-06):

### Motor Control Progress Report #6

Skittle Sorter Project
Jaidon Lybbert, Motor Control Design Lead, EWU IEEE Student Chapter
Week of 08/09/20

Problem:
- Little control structure was in place for running the system. As a result, the system would run its test sequence the moment the code was flashed, with no start or stop inputs.
- Although the code was updated to facilitate adding a second motor, no code was in place to implement a second motor.
- The control code (sorter.c) lacked any substantive comments.
- The user interface team was in need of an accessible way to understand the motor control code to make use of its functions.
- The sequence that occurs when executing an interrupt was not understood

Research:
- Setting up interrupts on the tm4c
- http://users.ece.utexas.edu/~valvano/Volume1/E-Book/C12_Interrupts.htm
- Context switching, kernels
- https://dmitryfrank.com/articles/how_i_ended_up_writing_my_own_kernel
- https://en.wikipedia.org/wiki/Kernel_(operating_system)
- RISC
- https://en.wikipedia.org/wiki/Reduced_instruction_set_computer
- SoCs
- https://en.wikipedia.org/wiki/System_on_a_chip
- https://electronics.stackexchange.com/questions/16828/microcontroller-vs-syste m-on-chip (https://electronics.stackexchange.com/questions/16828/microcontroller-vs-system-on-chip)
- Assembly language
- https://www.tutorialspoint.com/assembly_programming/assembly_basic_syntax.h tm (https://www.tutorialspoint.com/assembly_programming/assembly_basic_syntax.htm)
- Linker scripts
- https://wiki.osdev.org/Linker_Scripts

Action:
- Added start input to the testing sequence, and different modes of testing for separate hardware configurations
- Initialized ports and defines for second motor output
- Added descriptive comments throughout the control/testing code
- Drew up function call diagrams for relevant functions in the stepper code

Value:
- The motor control code is now considered functionally complete, and ready to be integrated with the rest of the system as they are completed
- Through comments and documentation, interfacing with the motor control code has been made easier for other teams
- A better understanding of interrupt execution, lower levels of programming, and the linking process may help to avoid bugs in the future

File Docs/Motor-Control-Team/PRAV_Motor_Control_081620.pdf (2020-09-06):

### Motor Control Progress Report #7

Skittle Sorter Project
Jaidon Lybbert, Motor Control Design Lead, EWU IEEE Student Chapter
Week of 08/16/20

Problem:
- The motor driver circuit using the l293b has been prototyped on a breadboard, which is a temporary solution, and has poor cooling, causing the chip to melt the breadboard when run for extended periods of time
- Motor control development has been done on a separate branch on GitHub for several weeks, and merge conflicts have shown up between the motor control branch and the master branch
- Motor control progress reports have been in scattered formats and memos without a defined format

Research:
- Resolving merge conflicts on GitHub
- https://docs.github.com/en/github/collaborating-with-issues-and-pull-requests/res olving-a-merge-conflict-using-the-command-line (https://docs.github.com/en/github/collaborating-with-issues-and-pull-requests/resolving-a-merge-conflict-using-the-command-line)
- Using KiCad to design PCBs
- See “Getting Started with KiCad” at the end of this report

Action:
- Researched PCB design and manufacturing
- Learned KiCad
- Designed and redesigned PCB for the driver circuit
- See “Stepper Driver PCB Design” and “Stepper Driver PCB Iterations” at the end of this report
- Merged the motor control branch to the master branch on GitHub
- Consolidated weeks of notes into polished progress reports

Value:
- Merging multiple weeks of changes onto the master branch finalizes the changes and brings our main development branch up to date
- A PCB for the driver circuit will allow us to clean up our hardware to make it more presentable, easier to use, and allows for better cooling of the ICs
- Knowledge of designing PCBs will aid in future projects that require them
- A clear history of progress with the motor control will help new team members get up to date, as well as communicate new changes with other teams

### Stepper Driver PCB Design

Jaidon Lybbert, Motor Control Design Lead, EWU IEEE Student Chapter 08/23/20

This document describes the current stepper motor driver PCB design.

3D View:


Fig. 1: Current version of the driver PCB. The outer ICs are l293B chips, and the center IC is an l293D chip. The l293Bs have 2 external 1N4001 flyback diodes for each of their 4 output pins (J5, J6). The connectors at the top end of each IC are the logical inputs (J2, J7, J3) and connector J4 has one active high enable pin for each IC. Each IC has one 0.22uF bypass capacitor for its logic power supply input.

PCB Specifications:
- Layers: 2
- Dimensions: 44.45 x 76.20mm
- Thickness: 1.6mm
- Copper weight: 2 Oz.

Components List:

"Source:" | "C:\Users\Jaidon Lybbert\Documents\Classwork\EENG250\Lab0\MotorDriver\Motor_Driver\Motor_Driver.sch"
"Date:" | "8/23/20 2:54:10 PM"
"Tool:" | "Eeschema (5.1.5-108-gad11b7ebd)-1"
"Component Count:" | "30"
"Ref" | "Value" | "Part" | "Footprint" | "Description" "Vendor"
"C1" | "0.22uF" | "Device:C_Small" | "Capacitor_THT:C_Disc_D5.1mm_W3.2mm_P5.00mm" | "Unpolarized capacitor, small symbol" ""
"C2" | "0.22uF" | "Device:C_Small" | "Capacitor_THT:C_Disc_D5.1mm_W3.2mm_P5.00mm" | "Unpolarized capacitor, small symbol" ""
"C3" | "0.22uF" | "Device:C_Small" | "Capacitor_THT:C_Disc_D5.1mm_W3.2mm_P5.00mm" | "Unpolarized capacitor, small symbol" ""
"D1" | "1N4001" | "Diode:1N4001" | "Diode_THT:D_DO-41_SOD81_P10.16mm_Horizontal" | "50V 1A General Purpose Rectifier Diode, DO-41"
"D2" | "1N4001" | "Diode:1N4001" | "Diode_THT:D_DO-41_SOD81_P10.16mm_Horizontal" | "50V 1A General Purpose Rectifier Diode, DO-41"
"D3" | "1N4001" | "Diode:1N4001" | "Diode_THT:D_DO-41_SOD81_P10.16mm_Horizontal" | "50V 1A General Purpose Rectifier Diode, DO-41"
"D4" | "1N4001" | "Diode:1N4001" | "Diode_THT:D_DO-41_SOD81_P10.16mm_Horizontal" | "50V 1A General Purpose Rectifier Diode, DO-41"
"D5" | "1N4001" | "Diode:1N4001" | "Diode_THT:D_DO-41_SOD81_P10.16mm_Horizontal" | "50V 1A General Purpose Rectifier Diode, DO-41"
"D6" | "1N4001" | "Diode:1N4001" | "Diode_THT:D_DO-41_SOD81_P10.16mm_Horizontal" | "50V 1A General Purpose Rectifier Diode, DO-41"
"D7" | "1N4001" | "Diode:1N4001" | "Diode_THT:D_DO-41_SOD81_P10.16mm_Horizontal" | "50V 1A General Purpose Rectifier Diode, DO-41"
"D8" | "1N4001" | "Diode:1N4001" | "Diode_THT:D_DO-41_SOD81_P10.16mm_Horizontal" | "50V 1A General Purpose Rectifier Diode, DO-41"
"D9" | "1N4001" | "Diode:1N4001" | "Diode_THT:D_DO-41_SOD81_P10.16mm_Horizontal" | "50V 1A General Purpose Rectifier Diode, DO-41"
"D10" | "1N4001" | "Diode:1N4001" | "Diode_THT:D_DO-41_SOD81_P10.16mm_Horizontal" | "50V 1A General Purpose Rectifier Diode, DO-41"
"D11" | "1N4001" | "Diode:1N4001" | "Diode_THT:D_DO-41_SOD81_P10.16mm_Horizontal" | "50V 1A General Purpose Rectifier Diode, DO-41"
"D12" | "1N4001" | "Diode:1N4001" | "Diode_THT:D_DO-41_SOD81_P10.16mm_Horizontal" | "50V 1A General Purpose Rectifier Diode, DO-41"
"D13" | "1N4001" | "Diode:1N4001" | "Diode_THT:D_DO-41_SOD81_P10.16mm_Horizontal" | "50V 1A General Purpose Rectifier Diode, DO-41"
"D14" | "1N4001" | "Diode:1N4001" | "Diode_THT:D_DO-41_SOD81_P10.16mm_Horizontal" | "50V 1A General Purpose Rectifier Diode, DO-41"
"D15" | "1N4001" | "Diode:1N4001" | "Diode_THT:D_DO-41_SOD81_P10.16mm_Horizontal" | "50V 1A General Purpose Rectifier Diode, DO-41"
"D16" | "1N4001" | "Diode:1N4001" | "Diode_THT:D_DO-41_SOD81_P10.16mm_Horizontal" | "50V 1A General Purpose Rectifier Diode, DO-41"
"J1" | "Barrel_Jack""Connector:Barrel_Jack" "Connector_BarrelJack:BarrelJack_Horizontal" | "DC Barrel Jack" | ""
"J2" | "Conn_01x04_Female" | "Connector:Conn_01x04_Female" | "Connector_JST:JST_EH_B4B-EH-A_1x04_P2.50mm_Vertical"
"J3" | "Conn_01x04_Female" | "Connector:Conn_01x04_Female" | "Connector_JST:JST_EH_B4B-EH-A_1x04_P2.50mm_Vertical"
"J4" | "Conn_01x03_Female" | "Connector:Conn_01x03_Female" | "Connector_JST:JST_EH_B3B-EH-A_1x03_P2.50mm_Vertical"
"J5" | "Conn_01x04_Male" | "Connector:Conn_01x04_Male" | "Connector_JST:JST_EH_B4B-EH-A_1x04_P2.50mm_Vertical"
"J6" | "Conn_01x04_Male" | "Connector:Conn_01x04_Male" | "Connector_JST:JST_EH_B4B-EH-A_1x04_P2.50mm_Vertical"
"J7" | "Conn_01x02_Female" | "Connector:Conn_01x02_Female" | "Connector_JST:JST_EH_B2B-EH-A_1x02_P2.50mm_Vertical"
"J8" | "Conn_01x02_Male" | "Connector:Conn_01x02_Male" | "Connector_JST:JST_EH_B2B-EH-A_1x02_P2.50mm_Vertical"
"U1" | "L293B" | "Driver_Motor:L293" | "Package_DIP:DIP-16_W7.62mm" | "Quadruple Half-H Drivers"""
"U2" | "L293B" | "Driver_Motor:L293" | "Package_DIP:DIP-16_W7.62mm" | "Quadruple Half-H Drivers"""
"U3" | "L293D" | "Driver_Motor:L293D" | "Package_DIP:DIP-16_W7.62mm" | "Quadruple Half-H Drivers"""

Additional notes:
- The l293B chips require heatsinks


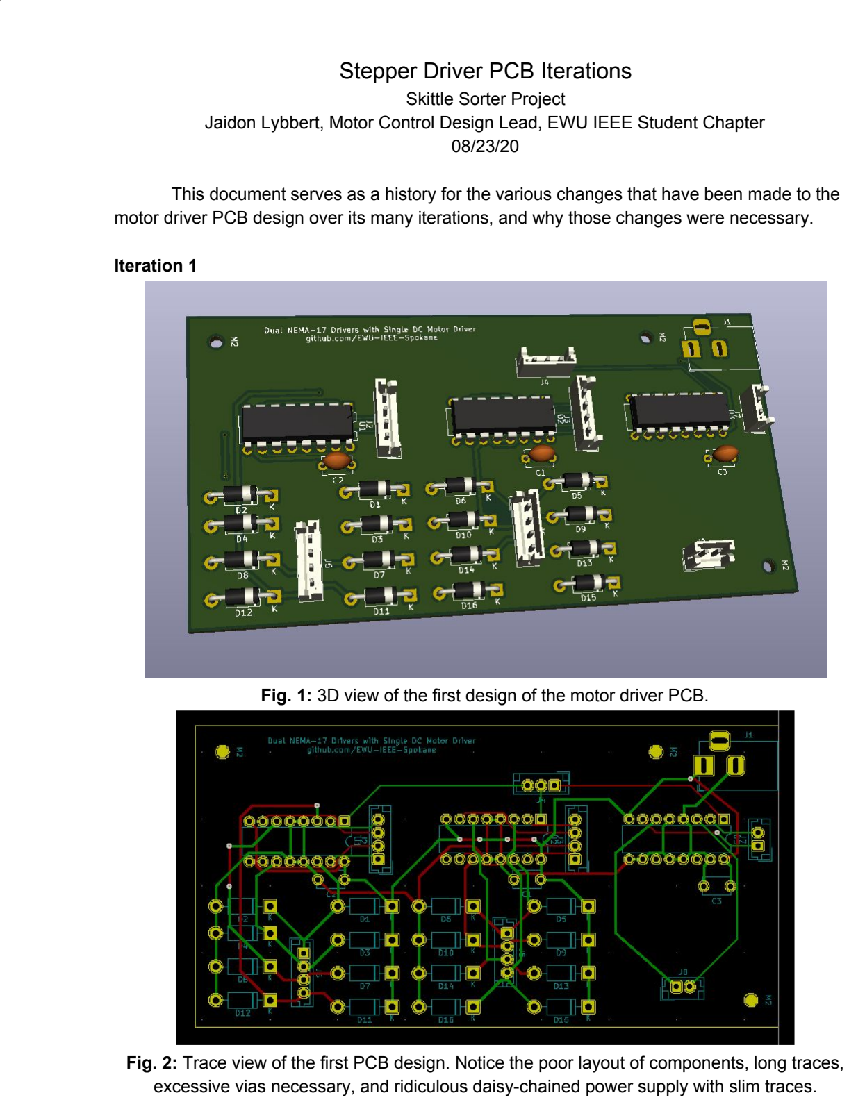
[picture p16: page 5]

### Stepper Driver PCB Iterations

Jaidon Lybbert, Motor Control Design Lead, EWU IEEE Student Chapter 08/23/20

This document serves as a history for the various changes that have been made to the motor driver PCB design over its many iterations, and why those changes were necessary.

Iteration 1

Fig. 1: 3D view of the first design of the motor driver PCB.

Fig. 2: Trace view of the first PCB design. Notice the poor layout of components, long traces, excessive vias necessary, and ridiculous daisy-chained power supply with slim traces.

Issues with iteration 1:
- The power supply is located at one end of the board, and the ICs are daisy-chained together. When one IC draws a lot of current, the ICs up the chain will likely experience a lot of noise at both their logic supply, and power supply inputs.
- The trace widths for the power supply pins are not wide enough. They would burn and short with less than 1 amp of current. Since the chips are daisy-chained, a lot more than 1 amp (closer to 4) could be drawn through these traces.
- There is a lot of unused space on the board. Traces are long, which will increase noise and thermal losses.
- The outputs are far from the ICs and placed in an awkward position, making running traces to them difficult (there are two output pins on either side of each IC) and long.

Iteration 2

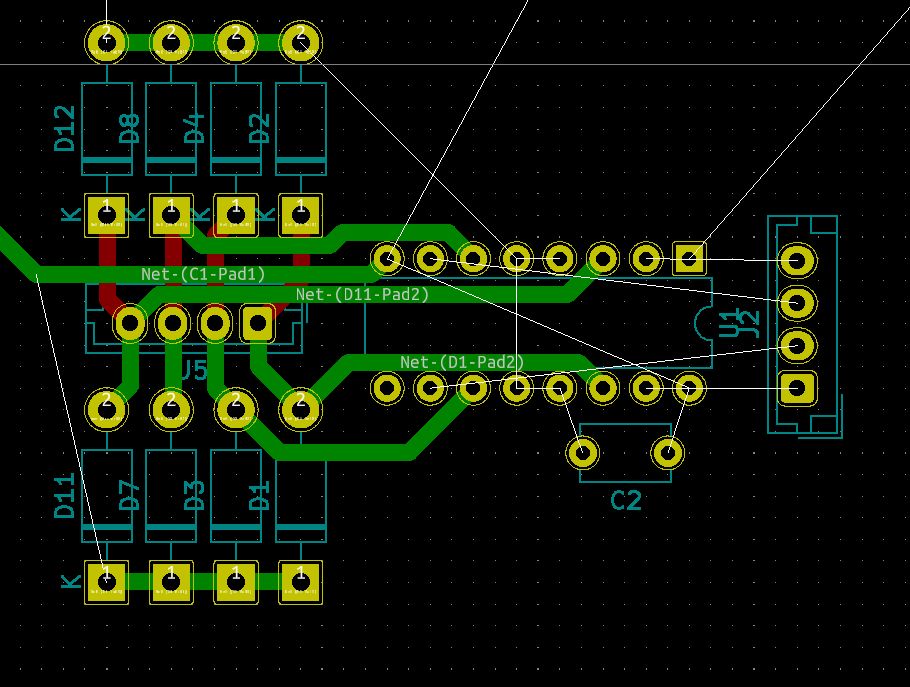
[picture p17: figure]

Figure 3: The second iteration of the PCB design. At this stage I focused only on the layout of one L293B, since it would be duplicated for the other. When I noticed issues, I stopped and restarted instead of carrying through and finishing the board.

Improvements in iteration 2:
- The trace widths are now wide enough to carry the desired current, so long as ICs are not daisy-chained, and a copper weight of 2 oz is used.
- The placement of the output pins at the bottom of the IC, instead of the side, allows for shorter, more direct connections between the IC and connector.
- Traces around the heatsink/ground pins are eliminated, allowing better thermal dissipation across the ground planes.
- Due to the better layout, no vias are necessary, and the footprint is reduced in size.

Issues with iteration 2:
- The flyback diodes from output to VCC are on the opposite side of the IC from the VCC input pin. This means a high current trace would have to be run around the board or underneath it. Rotating the flyback diode/output connector section 180° would allow a shorter direct connection.

Iteration 3

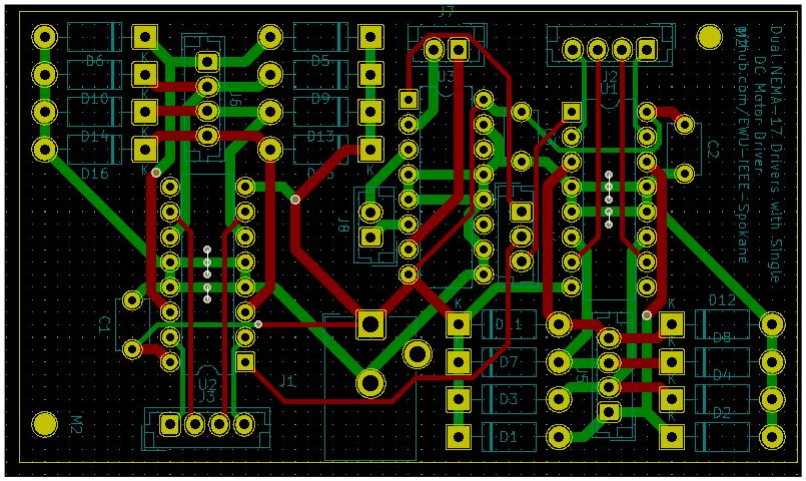
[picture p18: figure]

Figure 4: Iteration 3 of the driver PCB. A small layout means high current traces are kept minimized and direct, and noise is reduced.

Iteration 3 improvements:
- Total area is reduced from 64 cm²

to 34 cm² when compared to iteration 1.
- Power connections are direct (the daisy-chaining seen between U1 and U3 does not occur in the design, that is the one modification not shown here).
- Thermal vias are included to conduct heat from the center of each l293B to the ground plane on the backside of the board.
- Total number of vias (excluding thermal vias) is reduced from 9 to 4.

Iteration 3 issues:
- This design will require external heatsinks for the l293B chips as there is simply not enough copper on the ground planes to dissipate the heat

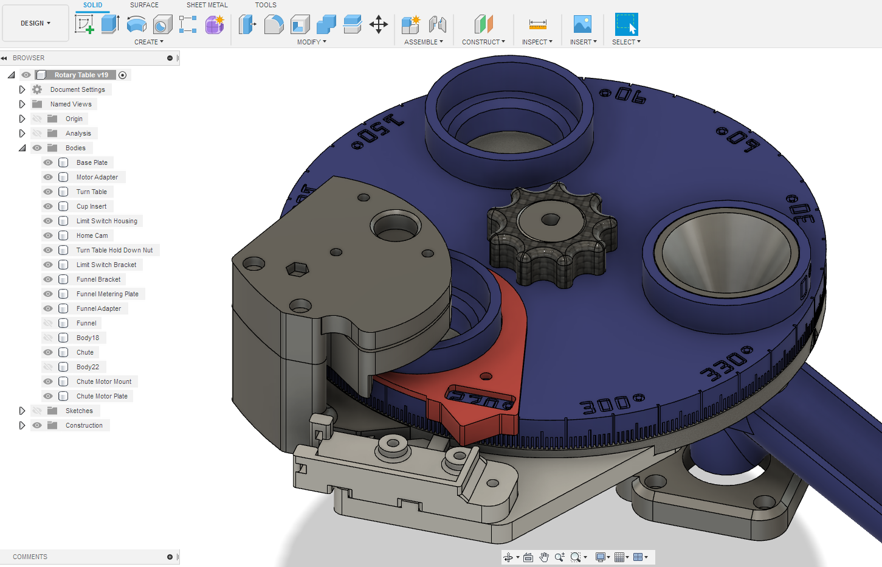
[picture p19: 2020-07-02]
Docs/Mechanical-Engineers/Mechanical Design Detail.PNG

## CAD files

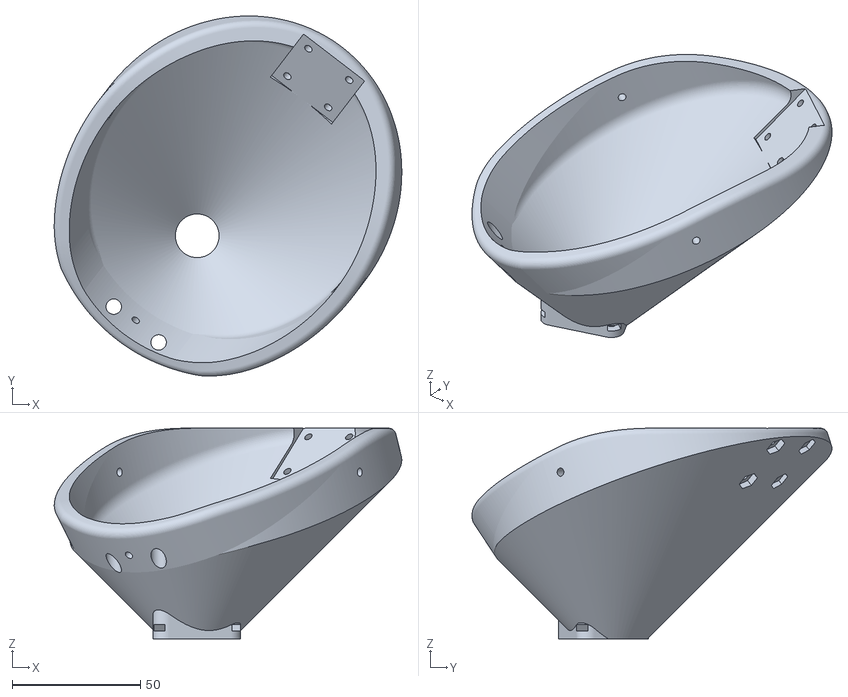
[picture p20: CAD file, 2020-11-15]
3D_Models/Improved Funnel.stl
135.3 x 140.1 x 82.0

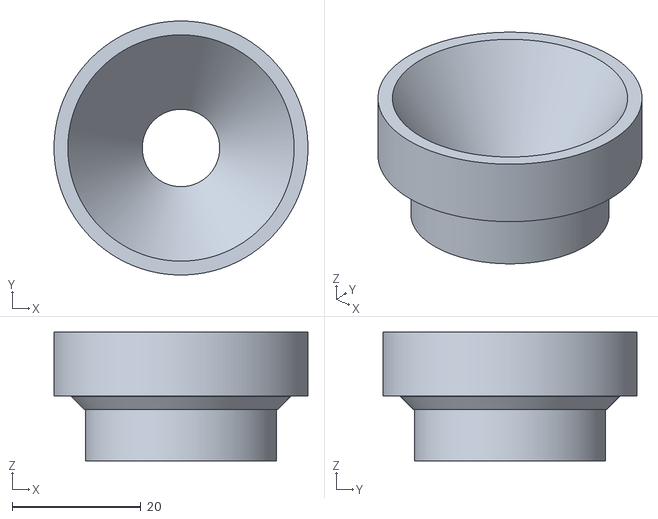
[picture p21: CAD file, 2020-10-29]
3D_Models/Cup Insert.stl
39.4 x 39.4 x 20.0

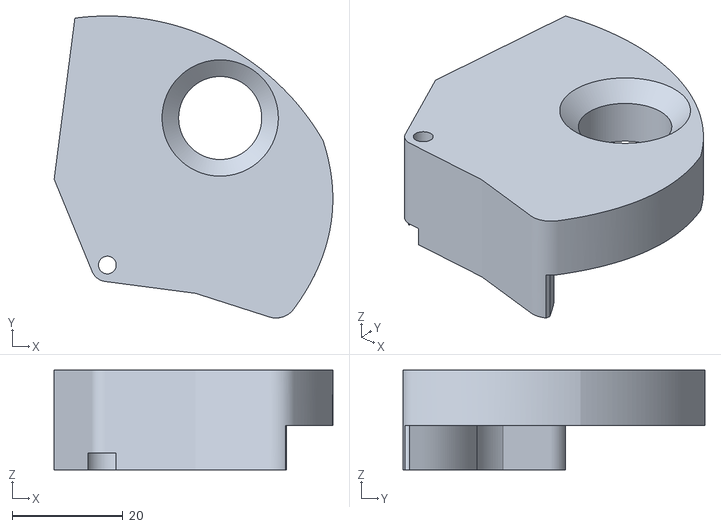
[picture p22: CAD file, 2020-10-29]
3D_Models/Funnel Metering Plate 3mm Chamfer.stl
50.4 x 54.6 x 18.0

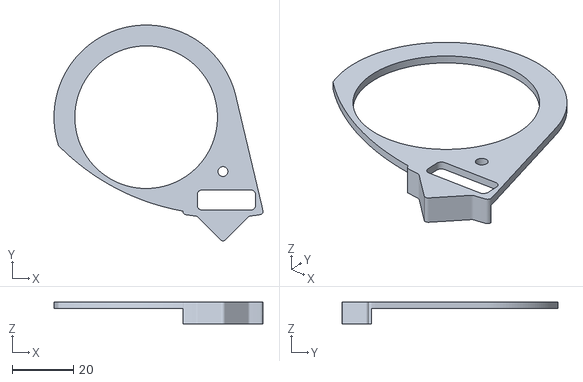
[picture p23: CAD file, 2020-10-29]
3D_Models/Home Cam.stl
68.0 x 70.3 x 7.00

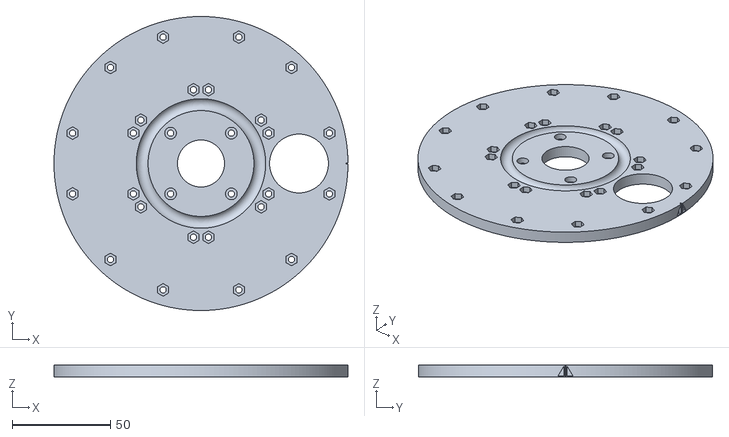
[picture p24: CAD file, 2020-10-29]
3D_Models/Base Plate.stl
150.0 x 150.0 x 6.00

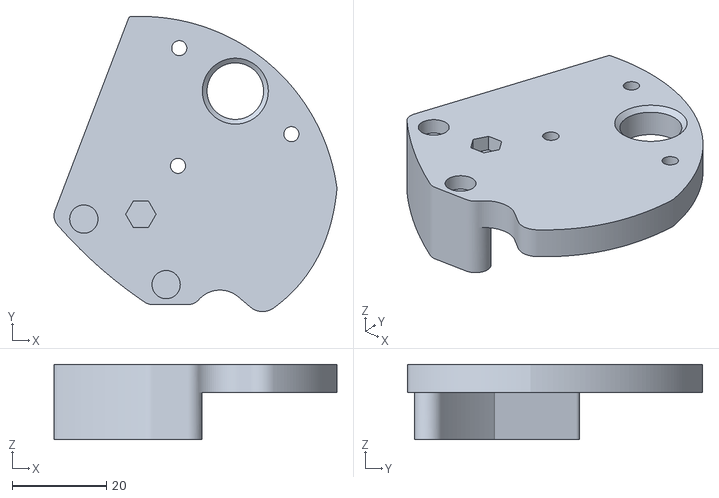
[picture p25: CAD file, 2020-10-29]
3D_Models/Funnel Adapter.stl
60.1 x 62.7 x 16.0

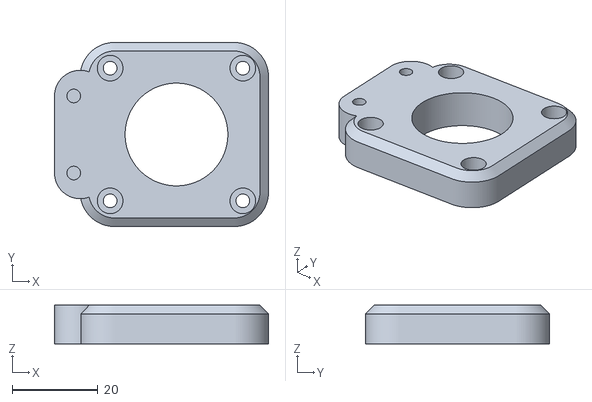
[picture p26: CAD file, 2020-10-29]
3D_Models/Chute Motor Plate.stl
50.0 x 43.0 x 9.00

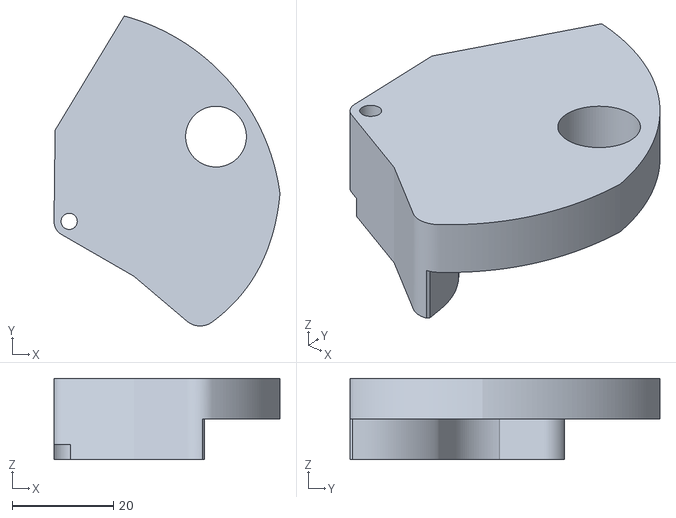
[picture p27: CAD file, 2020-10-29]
3D_Models/Funnel Metering Plate.stl
44.6 x 61.2 x 16.0

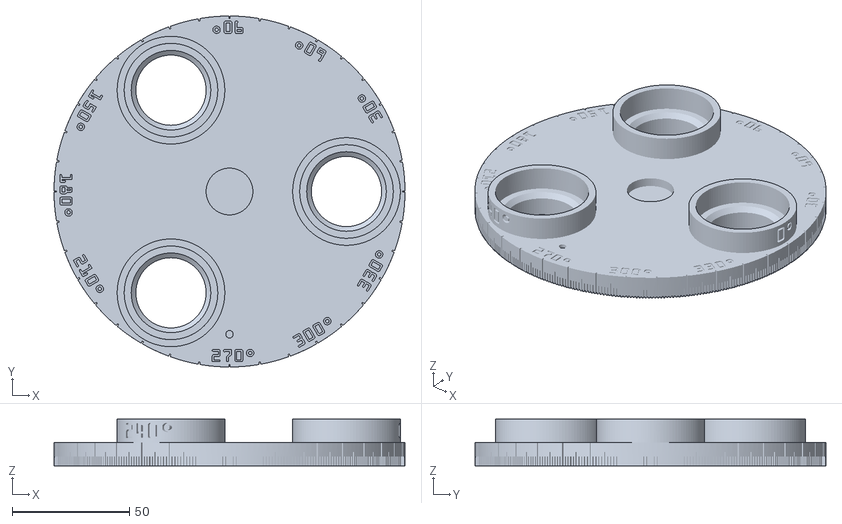
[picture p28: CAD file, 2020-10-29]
3D_Models/Turn Table.stl
150.0 x 150.0 x 20.0

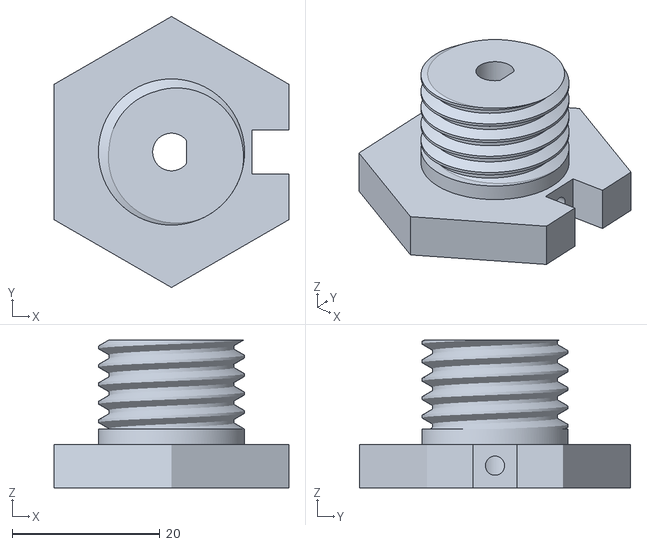
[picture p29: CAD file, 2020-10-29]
3D_Models/Motor Adapter.stl
31.8 x 36.7 x 20.0

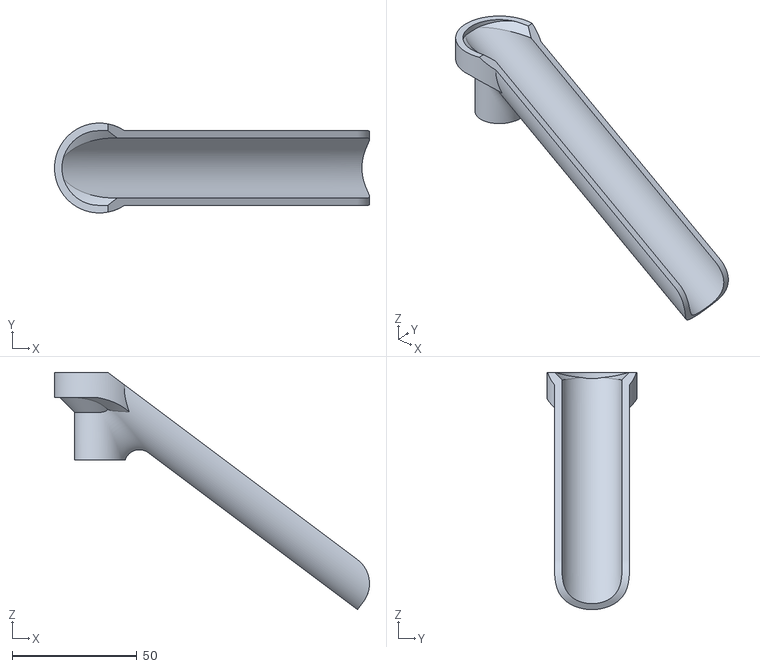
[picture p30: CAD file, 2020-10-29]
3D_Models/Chute.stl
126.2 x 36.0 x 95.0

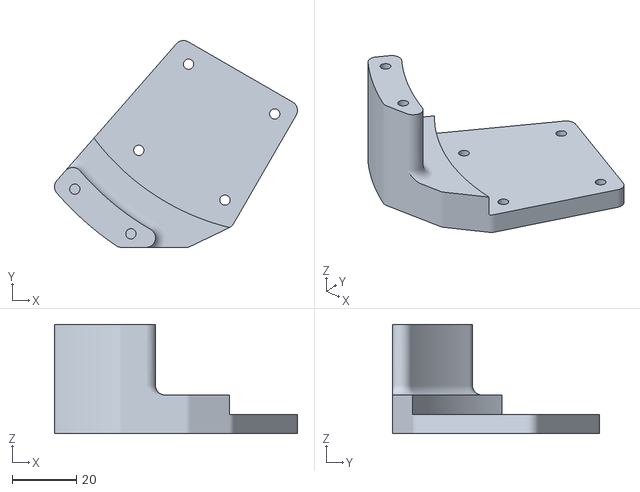
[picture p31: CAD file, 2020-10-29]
3D_Models/Funnel Bracket Improved.stl
75.7 x 64.5 x 34.0

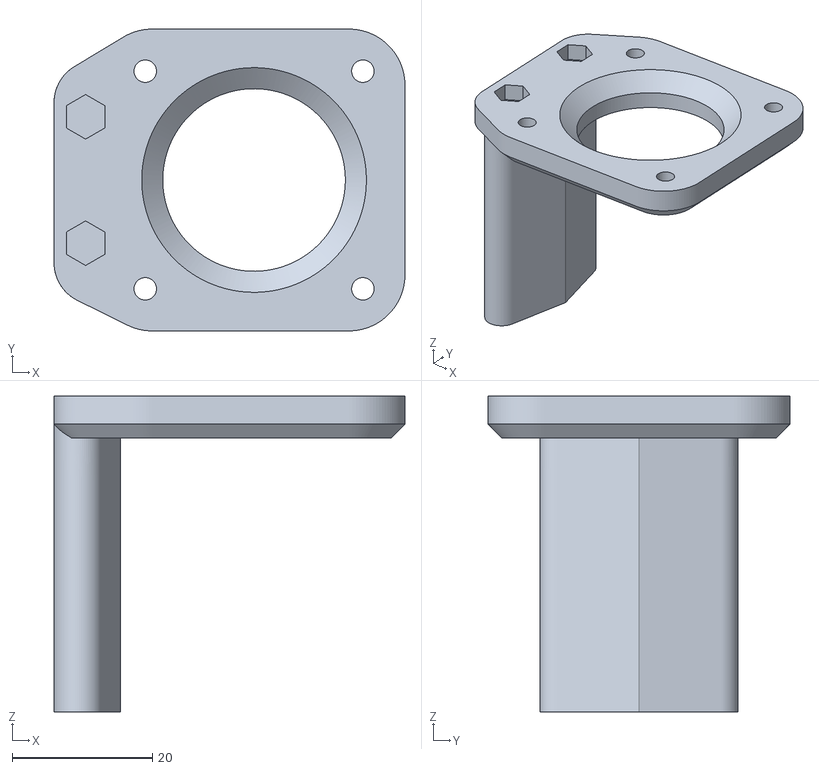
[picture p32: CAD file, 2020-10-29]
3D_Models/Chute Motor Mount.stl
50.0 x 43.0 x 45.0

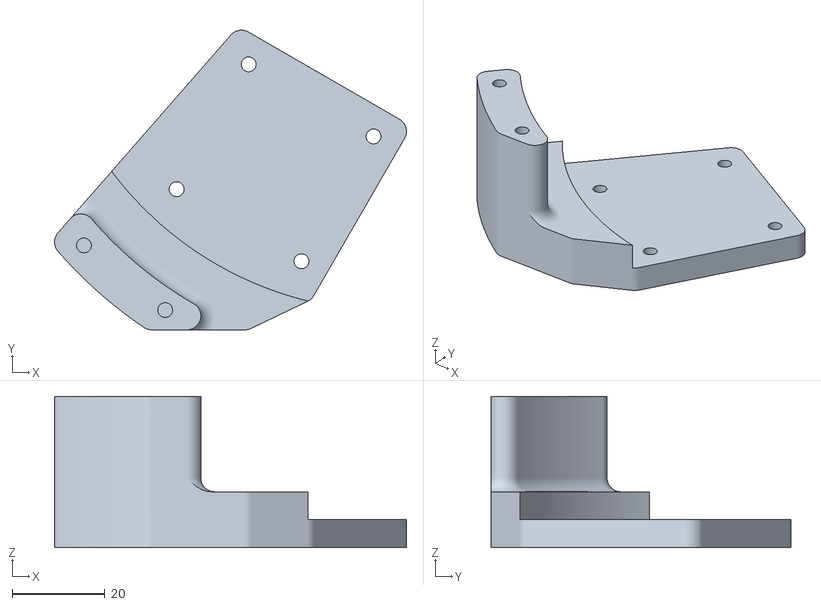
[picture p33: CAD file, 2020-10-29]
3D_Models/Funnel Bracket.stl
75.7 x 64.5 x 32.5

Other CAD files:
3D_Models/Funnel Metering Plate Improved.stl
3D_Models/Limit Switch Housing.stl
3D_Models/Frame Adapter.stl
3D_Models/Blocking Plate.stl
3D_Models/Funnel Adapter Improved.stl
3D_Models/Funnel.stl
3D_Models/Limit Switch Bracket.stl
3D_Models/Turn Table Hold Down Nut.stl

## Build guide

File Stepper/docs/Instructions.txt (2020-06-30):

(1) Clone repository, or just download the Stepper directory
(2) Open a terminal on your desktop
(3) CD into the Stepper folder
(4) Run the "make" command
(5) Make sure that the Tm4c is plugged in
(6) Run the "lm4flash stepper.axf" command
(7) The firmware is now flashed to your device

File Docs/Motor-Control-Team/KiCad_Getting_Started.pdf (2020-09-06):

Jaidon Lybbert
August 19th, 2020
EWU IEEE Student Chapter

### Getting Started Designing Custom PCBs in KiCad

Presented here are all the resources you need to layout and package a custom PCB design to be sent in for manufacturing.

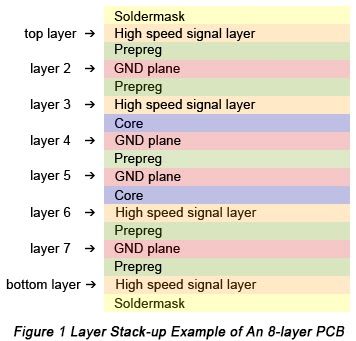
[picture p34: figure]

What is a PCB?
- Read the “Overview” section on Wikipedia (https://en.wikipedia.org/wiki/Printed_circuit_board)
- Read this article (https://www.bitweenie.com/listings/pcb-layers/) about different PCB layers
- Watch this video (https://www.youtube.com/watch?v=ljOoGyCso8s) to see the manufacturing process

Some key points and terms to be familiar with:
- Traces, copper weights, and their current carrying capacities
- Thermal stresses
- Ground/power planes and their applications
- Silk screens, solder masks, vias, prepreg

How do I design one?
- Download KiCad (https://kicad-pcb.org/)
- Come up with an idea for a circuit
- Keep these tips (https://www.allaboutcircuits.com/technical-articles/practical-pcb-layout-tips/) in mind
- Use this trace width calculator (https://www.4pcb.com/trace-width-calculator.html)
- Watch this video (https://www.youtube.com/watch?v=-tN14xlWWmA) while following along with your own design

Who do I send my design to?
- There are an uncountable number of manufacturers
- One cheap one I found is JLCPCB (https://jlcpcb.com/)

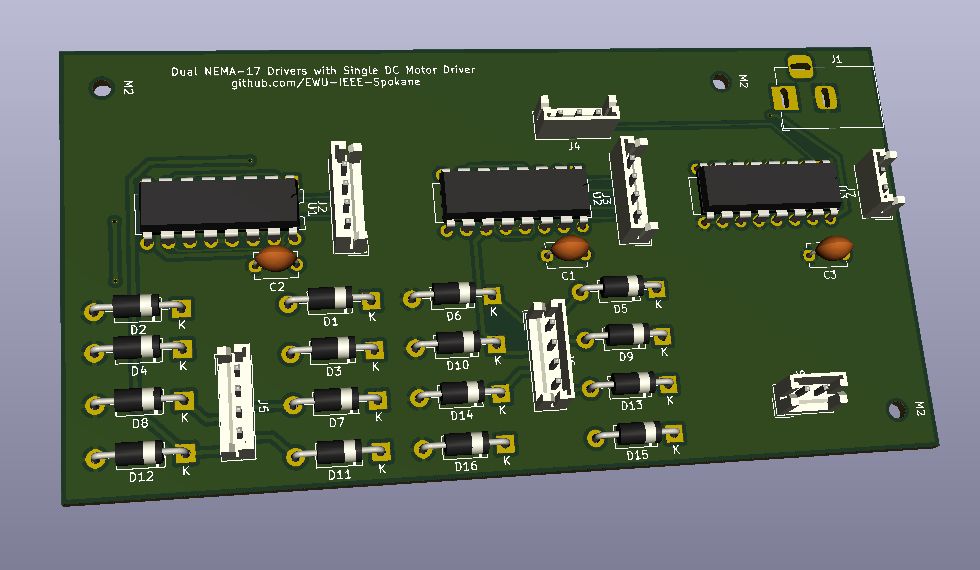
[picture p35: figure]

Fig. 2: 3D rendering of a KiCad PCB Further Learning (feel free to add to this list)
- SparkFun electronics has a couple youtube videos (https://www.youtube.com/watch?v=NJKZZArjdg8) with design tips

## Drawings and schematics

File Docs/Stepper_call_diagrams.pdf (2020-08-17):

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

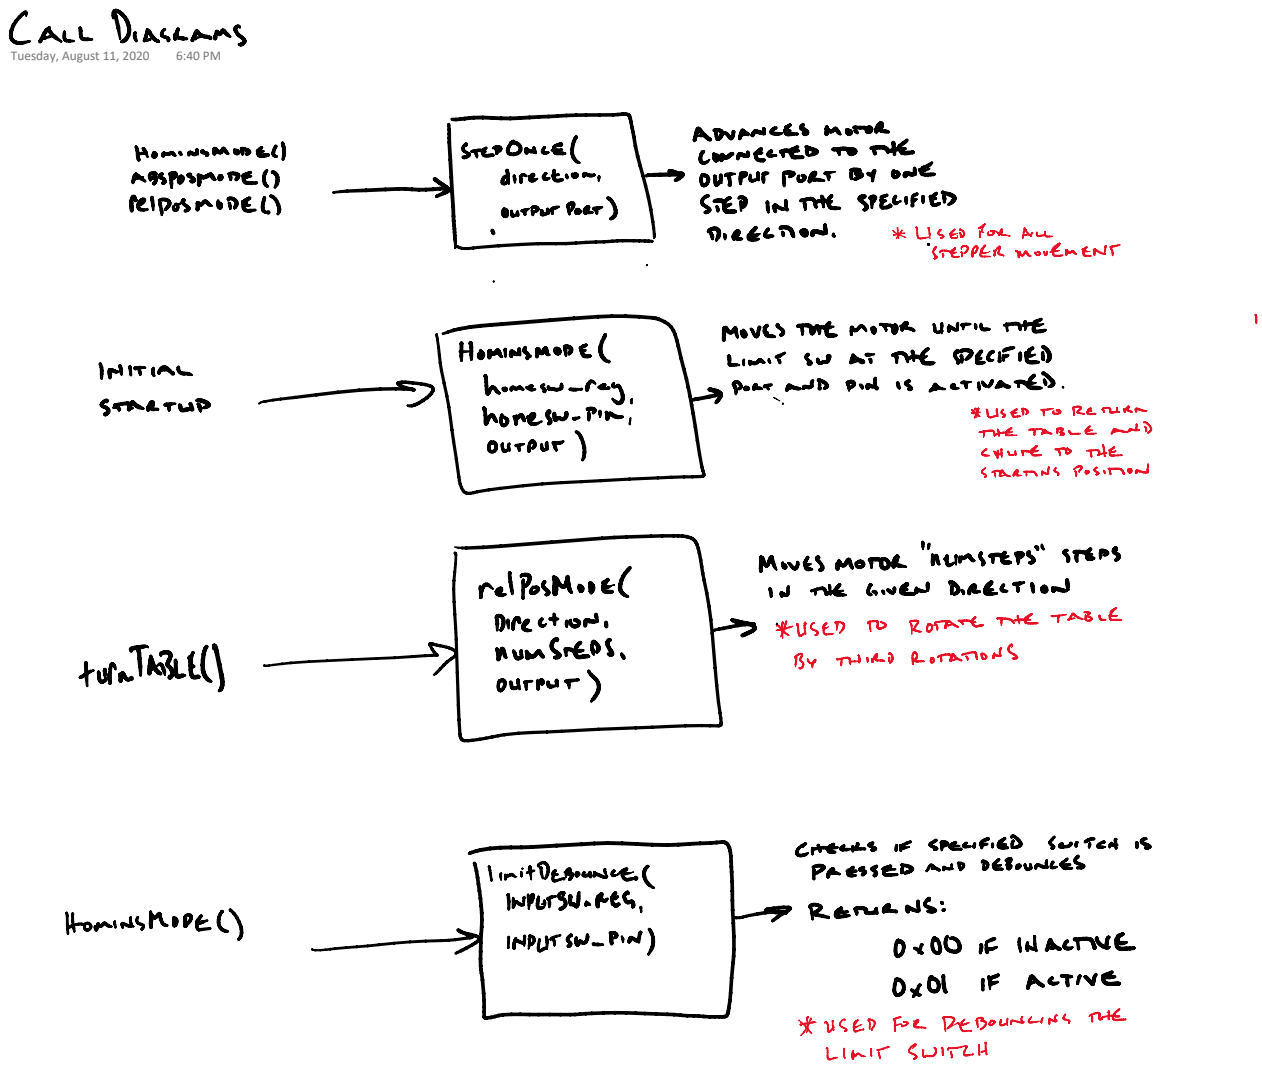
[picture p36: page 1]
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

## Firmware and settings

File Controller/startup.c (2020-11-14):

//*****************************************************************************
//
// startup.c - Startup code for use with GNU tools.
//
// Copyright (c) 2012-2017 Texas Instruments Incorporated.  All rights reserved.
// Software License Agreement
// 
// Texas Instruments (TI) is supplying this software for use solely and
// exclusively on TI's microcontroller products. The software is owned by
// TI and/or its suppliers, and is protected under applicable copyright
// laws. You may not combine this software with "viral" open-source
// software in order to form a larger program.
// 
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
// This is part of revision 2.1.4.178 of the EK-TM4C123GXL Firmware Package.
//
// This file inlcudes a switch handler for interrups (EENG260 Final task 2 and 3)
// The changes are in the vector table for port F, including stdbool.h, prototyping the handler,
// and the switch_handler method at the bottom of the code. 
//
//*****************************************************************************

#include <stdint.h>
#include <stdbool.h>    //Boolean for flag used in switch handler
#include "led.h"
#include "sorter_init.h"
/* #include "inc/hw_nvic.h" */
#define NVIC_CPAC               0xE000ED88  // Coprocessor Access Control
#define NVIC_CPAC_CP11_M        0x00C00000  // CP11 Coprocessor Access
                                            // Privilege
#define NVIC_CPAC_CP11_FULL     0x00C00000  // Full Access
#define NVIC_CPAC_CP10_M        0x00300000  // CP10 Coprocessor Access
                                            // Privilege
#define NVIC_CPAC_CP10_FULL     0x00300000  // Full Access

/* #include "inc/hw_types.h" */
#define HWREG(x)                                                              \
        (*((volatile uint32_t *)(x)))

//*****************************************************************************
//
// Forward declaration of the default fault handlers.
//
//*****************************************************************************
void ResetISR(void);
static void NmiSR(void);
static void FaultISR(void);
static void IntDefaultHandler(void);
static void StartStopHandler(void);

//*****************************************************************************
//
// The entry point for the application.
//
//*****************************************************************************
extern int main(void);

//*****************************************************************************
//
// Reserve space for the system stack.
//
//*****************************************************************************
static uint32_t pui32Stack[128];

//*****************************************************************************
//
// The vector table.  Note that the proper constructs must be placed on this to
// ensure that it ends up at physical address 0x0000.0000.
//
//*****************************************************************************
__attribute__ ((section(".isr_vector")))
void (* const g_pfnVectors[])(void) =
{
    (void (*)(void))((uint32_t)pui32Stack + sizeof(pui32Stack)),
                                            // The initial stack pointer
    ResetISR,                               // The reset handler
    NmiSR,                                  // The NMI handler
    FaultISR,                               // The hard fault handler
    IntDefaultHandler,                      // The MPU fault handler
    IntDefaultHandler,                      // The bus fault handler
    IntDefaultHandler,                      // The usage fault handler
    0,                                      // Reserved
    0,                                      // Reserved
    0,                                      // Reserved
    0,                                      // Reserved
    IntDefaultHandler,                      // SVCall handler
    IntDefaultHandler,                      // Debug monitor handler
    0,                                      // Reserved
    IntDefaultHandler,                      // The PendSV handler
    IntDefaultHandler,                      // The SysTick handler
    IntDefaultHandler,                      // GPIO Port A
    StartStopHandler,                       // GPIO Port B
    IntDefaultHandler,                      // GPIO Port C
    IntDefaultHandler,                      // GPIO Port D
    IntDefaultHandler,                      // GPIO Port E
    IntDefaultHandler,                      // UART0 Rx and Tx
    IntDefaultHandler,                      // UART1 Rx and Tx
    IntDefaultHandler,                      // SSI0 Rx and Tx
    IntDefaultHandler,                      // I2C0 Master and Slave
    IntDefaultHandler,                      // PWM Fault
    IntDefaultHandler,                      // PWM Generator 0
    IntDefaultHandler,                      // PWM Generator 1
    IntDefaultHandler,                      // PWM Generator 2
    IntDefaultHandler,                      // Quadrature Encoder 0
    IntDefaultHandler,                      // ADC Sequence 0
    IntDefaultHandler,                      // ADC Sequence 1
    IntDefaultHandler,                      // ADC Sequence 2
    IntDefaultHandler,                      // ADC Sequence 3
    IntDefaultHandler,                      // Watchdog timer
    IntDefaultHandler,                      // Timer 0 subtimer A
    IntDefaultHandler,                      // Timer 0 subtimer B
    IntDefaultHandler,                      // Timer 1 subtimer A
    IntDefaultHandler,                      // Timer 1 subtimer B
    IntDefaultHandler,                      // Timer 2 subtimer A
    IntDefaultHandler,                      // Timer 2 subtimer B
    IntDefaultHandler,                      // Analog Comparator 0
    IntDefaultHandler,                      // Analog Comparator 1
    IntDefaultHandler,                      // Analog Comparator 2
    IntDefaultHandler,                      // System Control (PLL, OSC, BO)
    IntDefaultHandler,                      // FLASH Control
    IntDefaultHandler,                      // GPIO Port F
    IntDefaultHandler,                      // GPIO Port G
    IntDefaultHandler,                      // GPIO Port H
    IntDefaultHandler,                      // UART2 Rx and Tx
    IntDefaultHandler,                      // SSI1 Rx and Tx
    IntDefaultHandler,                      // Timer 3 subtimer A
    IntDefaultHandler,                      // Timer 3 subtimer B
    IntDefaultHandler,                      // I2C1 Master and Slave
    IntDefaultHandler,                      // Quadrature Encoder 1
    IntDefaultHandler,                      // CAN0
    IntDefaultHandler,                      // CAN1
    0,                                      // Reserved
    0,                                      // Reserved
    IntDefaultHandler,                      // Hibernate
    IntDefaultHandler,                      // USB0
    IntDefaultHandler,                      // PWM Generator 3
    IntDefaultHandler,                      // uDMA Software Transfer
    IntDefaultHandler,                      // uDMA Error
    IntDefaultHandler,                      // ADC1 Sequence 0
    IntDefaultHandler,                      // ADC1 Sequence 1
    IntDefaultHandler,                      // ADC1 Sequence 2
    IntDefaultHandler,                      // ADC1 Sequence 3
    0,                                      // Reserved
    0,                                      // Reserved
    IntDefaultHandler,                      // GPIO Port J
    IntDefaultHandler,                      // GPIO Port K
    IntDefaultHandler,                      // GPIO Port L
    IntDefaultHandler,                      // SSI2 Rx and Tx
    IntDefaultHandler,                      // SSI3 Rx and Tx
    IntDefaultHandler,                      // UART3 Rx and Tx
    IntDefaultHandler,                      // UART4 Rx and Tx
    IntDefaultHandler,                      // UART5 Rx and Tx
    IntDefaultHandler,                      // UART6 Rx and Tx
    IntDefaultHandler,                      // UART7 Rx and Tx
    0,                                      // Reserved
    0,                                      // Reserved
    0,                                      // Reserved
    0,                                      // Reserved
    IntDefaultHandler,                      // I2C2 Master and Slave
    IntDefaultHandler,                      // I2C3 Master and Slave
    IntDefaultHandler,                      // Timer 4 subtimer A
    IntDefaultHandler,                      // Timer 4 subtimer B
    0,                                      // Reserved
    0,                                      // Reserved
    0,                                      // Reserved
    0,                                      // Reserved
    0,                                      // Reserved
    0,                                      // Reserved
    0,                                      // Reserved
    0,                                      // Reserved
    0,                                      // Reserved
    0,                                      // Reserved
    0,                                      // Reserved
    0,                                      // Reserved
    0,                                      // Reserved
    0,                                      // Reserved
    0,                                      // Reserved
    0,                                      // Reserved
    0,                                      // Reserved
    0,                                      // Reserved
    0,                                      // Reserved
    0,                                      // Reserved
    IntDefaultHandler,                      // Timer 5 subtimer A
    IntDefaultHandler,                      // Timer 5 subtimer B
    IntDefaultHandler,                      // Wide Timer 0 subtimer A
    IntDefaultHandler,                      // Wide Timer 0 subtimer B
    IntDefaultHandler,                      // Wide Timer 1 subtimer A
    IntDefaultHandler,                      // Wide Timer 1 subtimer B
    IntDefaultHandler,                      // Wide Timer 2 subtimer A
    IntDefaultHandler,                      // Wide Timer 2 subtimer B
    IntDefaultHandler,                      // Wide Timer 3 subtimer A
    IntDefaultHandler,                      // Wide Timer 3 subtimer B
    IntDefaultHandler,                      // Wide Timer 4 subtimer A
    IntDefaultHandler,                      // Wide Timer 4 subtimer B
    IntDefaultHandler,                      // Wide Timer 5 subtimer A
    IntDefaultHandler,                      // Wide Timer 5 subtimer B
    IntDefaultHandler,                      // FPU
    0,                                      // Reserved
    0,                                      // Reserved
    IntDefaultHandler,                      // I2C4 Master and Slave
    IntDefaultHandler,                      // I2C5 Master and Slave
    IntDefaultHandler,                      // GPIO Port M
    IntDefaultHandler,                      // GPIO Port N
    IntDefaultHandler,                      // Quadrature Encoder 2
    0,                                      // Reserved
    0,                                      // Reserved
    IntDefaultHandler,                      // GPIO Port P (Summary or P0)
    IntDefaultHandler,                      // GPIO Port P1
    IntDefaultHandler,                      // GPIO Port P2
    IntDefaultHandler,                      // GPIO Port P3
    IntDefaultHandler,                      // GPIO Port P4
    IntDefaultHandler,                      // GPIO Port P5
    IntDefaultHandler,                      // GPIO Port P6
    IntDefaultHandler,                      // GPIO Port P7
    IntDefaultHandler,                      // GPIO Port Q (Summary or Q0)
    IntDefaultHandler,                      // GPIO Port Q1
    IntDefaultHandler,                      // GPIO Port Q2
    IntDefaultHandler,                      // GPIO Port Q3
    IntDefaultHandler,                      // GPIO Port Q4
    IntDefaultHandler,                      // GPIO Port Q5
    IntDefaultHandler,                      // GPIO Port Q6
    IntDefaultHandler,                      // GPIO Port Q7
    IntDefaultHandler,                      // GPIO Port R
    IntDefaultHandler,                      // GPIO Port S
    IntDefaultHandler,                      // PWM 1 Generator 0
    IntDefaultHandler,                      // PWM 1 Generator 1
    IntDefaultHandler,                      // PWM 1 Generator 2
    IntDefaultHandler,                      // PWM 1 Generator 3
    IntDefaultHandler                       // PWM 1 Fault
};

//*****************************************************************************
//
// The following are constructs created by the linker, indicating where the
// the "data" and "bss" segments reside in memory.  The initializers for the
// for the "data" segment resides immediately following the "text" segment.
//
//*****************************************************************************
extern uint32_t _ldata;
extern uint32_t _data;
extern uint32_t _edata;
extern uint32_t _bss;
extern uint32_t _ebss;

//*****************************************************************************
//
// This is the code that gets called when the processor first starts execution
// following a reset event.  Only the absolutely necessary set is performed,
// after which the application supplied entry() routine is called.  Any fancy
// actions (such as making decisions based on the reset cause register, and
// resetting the bits in that register) are left solely in the hands of the
// application.
//
//*****************************************************************************
void
ResetISR(void)
{
    uint32_t *pui32Src, *pui32Dest;

    //
    // Copy the data segment initializers from flash to SRAM.
    //
    pui32Src = &_ldata;
    for(pui32Dest = &_data; pui32Dest < &_edata; )
    {
        *pui32Dest++ = *pui32Src++;
    }

    //
    // Zero fill the bss segment.
    //
    __asm("    ldr     r0, =_bss\n"
          "    ldr     r1, =_ebss\n"
          "    mov     r2, #0\n"
          "    .thumb_func\n"
          "zero_loop:\n"
          "        cmp     r0, r1\n"
          "        it      lt\n"
          "        strlt   r2, [r0], #4\n"
          "        blt     zero_loop");

    //
    // Enable the floating-point unit.  This must be done here to handle the
    // case where main() uses floating-point and the function prologue saves
    // floating-point registers (which will fault if floating-point is not
    // enabled).  Any configuration of the floating-point unit using DriverLib
    // APIs must be done here prior to the floating-point unit being enabled.
    //
    // Note that this does not use DriverLib since it might not be included in
    // this project.
    //
    HWREG(NVIC_CPAC) = ((HWREG(NVIC_CPAC) &
                         ~(NVIC_CPAC_CP10_M | NVIC_CPAC_CP11_M)) |
                        NVIC_CPAC_CP10_FULL | NVIC_CPAC_CP11_FULL);

    //
    // Call the application's entry point.
    //
    main();
}

//*****************************************************************************
//
// This is the code that gets called when the processor receives a NMI.  This
// simply enters an infinite loop, preserving the system state for examination
// by a debugger.
//
//*****************************************************************************
static void
NmiSR(void)
{
    //
    // Enter an infinite loop.
    //
    while(1)
    {
    }
}

//*****************************************************************************
//
// This is the code that gets called when the processor receives a fault
// interrupt.  This simply enters an infinite loop, preserving the system state
// for examination by a debugger.
//
//*****************************************************************************
static void
FaultISR(void)
{
    //
    // Enter an infinite loop.
    //
    while(1)
    {
    }
}

//*****************************************************************************
//
// This is the code that gets called when the processor receives an unexpected
// interrupt.  This simply enters an infinite loop, preserving the system state
// for examination by a debugger.
//
//*****************************************************************************
static void
IntDefaultHandler(void)
{
    //
    // Go into an infinite loop.
    //
    while(1)
    {
    }
}

/* Interrupt handler for stop button */
static void 
StartStopHandler(void) 
{
    if (GPIO_PORTB_RIS & 0x80) { // If PB7 was pressed
        GPIO_PORTB_ICR |= 0x80; // clear stop bit on PB7
        while(!(GPIO_PORTB_RIS & 0x02)) { // While PB1 (start) has not been pressed
            blink(0x02); // Blink red
        }
        GPIO_PORTB_ICR |= 0x02; // Clear start bit
    } else if (GPIO_PORTB_RIS & 0x02) { // If PB1 has been pressed
       /* GPIO_PORTB_ICR |= 0x02; // clear start bit*/
       // Do nothing except leave the start bit set
    }
}

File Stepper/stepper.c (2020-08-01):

#include <stdint.h>
#include <stdlib.h>
#include "stepper.h"
#include "umc_init.h"

uint16_t cStep = 0; // Current step number; i.e. address for absolute positioning; 0 should be "home" position
uint8_t cState = 0;

// States in the 28byJ FSM
State_t byjFSM[4] = {
    {0, 0x04, {1, 3} },
    {1, 0x08, {2, 0} },
    {2, 0x10, {3, 1} },
    {3, 0x20, {0, 2} }
};

// States in the Nema-17 FSM
State_t nemaFSM[4] = {
    {0, 0x18, {1, 3} },
    {1, 0x28, {2, 0} },
    {2, 0x24, {3, 1} },
    {3, 0x14, {0, 2} }
};

// Half-stepping Nema-17 FSM
State_t nema2FSM[8] = {
    {0, 0x18, {1, 7} },
    {4, 0x08, {2, 0} },
    {1, 0x28, {3, 1} },
    {5, 0x20, {4, 2} },
    {2, 0x24, {5, 3} },
    {6, 0x04, {6, 4} },
    {3, 0x14, {7, 5} },
    {7, 0x10, {0, 6} }
};

// Quick and dirty busy-loop delay
// This will need updating to a more precise delay
void delayT(int maxCount) {
    for (volatile int j = 0; j < maxCount; j++) {continue;}
}

// Step the motor once
// Direction map: 0x00 = CW; 0x01 = CCW; 
void stepOnce(uint8_t direction) {
    cState = nema2FSM[cState].next[direction]; // Move to next state defined by direction
    *GPIO_PORTA_DATA_R = nema2FSM[cState].out;  // Output motor data defined in new state
    
    // Update cStep--this algorithm can be improved
    if (direction == DIRECTION_CCW) { 
        if (cStep-1 < 0) {         // wrap around
            cStep = MAX_STEP;
        } else {
            cStep--; 
        }
    } else { 
        if (cStep+1 == MAX_STEP) {  // wrap around
            cStep = 0;          
        } else { 
            cStep++; 
        }
    }                         
}

// Debounce a button input
// This function must be called at a high frequency to work
// Inverts the "input" variable after the button is released
void debounce(uint8_t* input, uint8_t* flag) {
    if (*GPIO_PORTF_DATA_R == 16) {             // switch unpressed
            delayT(1000);
            if (*GPIO_PORTF_DATA_R == 16 && *flag == 0) {
                *input = (~(*input))&0x01;      // invert input
                *flag = 1;
            }
    } else {
        *flag = 0;
    }
}


// Debounce limit switch
uint8_t limitDebounce() {
    if (HOME == 0x01) {       // If switch activated
        delayT(1000);         // Wait for bouncing to stop
        if (HOME == 0x01) {   // If switch still activated
            return 0x01;      // Report switch activated
        }
        return 0x00;          // Otherwise: switch is unactivated
    } else {
        return 0x00;
    }
}

// Homing Mode
void homingMode() { // data = 0000 00 & direction & limitSw
    while(MODE == 0 && (limitDebounce() == 0x00)) {          // while the mode is unchanged and the switch is unpressed
        stepOnce(DIRECTION);                                 // continuously step in the specified direction
        delayT(10000);
    }
    cStep = 0;                                               // reset current step #
}

// Absolute Positioning Mode 1
// Turns motor to specific step number CW from "home" position using shortest path
// This works for applications with full 360 range of motion
void absPosMode_360() {
    
    uint8_t direction = 0x00;

    // Determine shortest path from cStep to "number" step
    // This algorithm can definitely be improved
    if (NUMBER > cStep) {
        if ((NUMBER - cStep) < (MAX_STEP / 2)) {
            direction = DIRECTION_CW;
        } else {
            direction = DIRECTION_CCW;
        }
    } else {
        if ((cStep - NUMBER) < (MAX_STEP / 2)) {
            direction = DIRECTION_CCW;
        } else {
            direction = DIRECTION_CW;
        }
    }

    // Continuously stepOnce in determined direction until cStep=="data"
    while(cStep != NUMBER) {
        stepOnce(direction);
        delayT(10000);
    }
}


// Absolute Positioning Mode 2
// Turns motor to specific step number CW from "home" position across "pie slice" of rotation
// This works for motors with limited range of motion due to an obstruction
void absPosMode_Slice(uint8_t stepNum) {
    
    uint8_t direction = 0x00;

    // Determine shortest path from cStep to "data" step
    // This algorithm can definitely be improved
    if (stepNum > cStep) {
        direction = DIRECTION_CW;
    } else {
        direction = DIRECTION_CCW;
    }

    // Continuously stepOnce in determined direction until cStep=="data"
    while(cStep != stepNum) {
        stepOnce(direction);
        delayT(10000);
    }
}

// Relative Positioning Mode
// Turns motor a specified number of steps in specified direction
// No stop condition
void relPosMode(uint8_t direction, uint8_t numSteps) {
    for (int i = 0; i < numSteps; i++) {            
        stepOnce(direction);
        delayT(10000);
    }
}

void run(uint8_t mode) {
    uint8_t number = NUMBER;
    switch (MODE) {
        case 0 : // Homing mode
            homingMode();
            break;
        case 1 : // Absolute positioning mode full range
            absPosMode_360();
            break;
        case 2 : // Absolute positioning mode limited range
            absPosMode_Slice(number);
            break;
        case 3 : // Relative positioning mode
            relPosMode(DIRECTION, number);
            break;
    }
}

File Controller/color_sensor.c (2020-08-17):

#include <stdint.h>
#include <stdbool.h>
#include "color_sensor.h"
#include "led.h"
#include "i2c.h"
#include "uart.h"
#include "color_process.h"

void config_sensor() {
	//configure the color sensor registers by sending it addressed values over I2C
	//blink(0X8);
	//write_sensor(0x00, 0xE6);	//clear pending interrupts
	//write_sensor(0x00, 0x00);
	write_sensor(0x00, 0x01); //turn on sensor clock
	delay(1000000);	//allow setup time for sensor clock - at least 2.4ms (this delay is probably overkill)
	//blink(0x08); //blink green to show oscillators up
	write_sensor(0x0F, 0x1); //set gain to 1xs
	write_sensor(0x01, 0xC0);	//set integration time to 154ms
	write_sensor(0x00, 0x3); //turn on sensor ADC's with 0x2 (plus 0x1 to keep oscillators enabled)
	//blink(0x08); //blink green to show ADC's up

	/* single write version
	single_write(0x80);
	single_write(0x01);
	delay(1000000);
	single_write(0x03);
	*/
}


void write_sensor(uint8_t addressIn, uint8_t dataIn) {
	//write a single data byte to the addressed register in the sensor
	single_write(0x80|addressIn); 	//in first command byte, tell the sensor what register to move to (bit 7 enables commands)
	single_write(dataIn);	        //write data to the above register
}



uint8_t read_sensor(uint8_t addressIn) {
	//read a single data byte from the addressed register
	uint8_t data;

	single_write(0x80|addressIn);	//1000 0000 + 0x12
	data = single_read();
	return data;
}

void wait_on_adc() {
	//wait for the on chip ADC to be ready, check by polling status reg 0x13 bit 0 (0x1 = ADC Valid)
	uint8_t sensorStatus = 0x0;
	bool colorValid = false;

		while(!colorValid){
			//wait here until a valid result is obtained from the sensor
			sensorStatus = read_sensor(0x13); //read status register (8 bits)
			colorValid = (sensorStatus & 0x1);	//color is valid if bit 1 is true
			//blink(0x2); too much delay
		}
}

int read_colors() {
	//read each color register and return the collection of data
	uint16_t redData = 0x0;
	uint16_t greenData = 0x0;
	uint16_t blueData = 0x0;

	uint16_t whiteValue = 0x0;
	//uint16_t irValue = 0x0;
	uint16_t sum = 0x0;

	//float redValue = 0x0;
	//float greenValue = 0x0;
	//float blueValue = 0x0;
	wait_on_adc();

	//read color value registers and combine bytes:
	whiteValue = (read_sensor(0x15)<<8) + read_sensor(0x14);
	//wait_on_adc();

	redData = (read_sensor(0x17)<<8) + read_sensor(0x16);		//high byte plus low byte
	//wait_on_adc();
	greenData = (read_sensor(0x19)<<8) + read_sensor(0x18);
	//wait_on_adc();
	blueData = (read_sensor(0x1B)<<8) + read_sensor(0x1A);

	sum = redData + greenData + blueData;

	/*
	if(sum>whiteValue){
		irValue = (sum-whiteValue)/2;
	}else{
		irValue = 0;
	}
	*/

	//combine values into one data packet (like hex color value)? for now just read them out with UART
	uartwrite('R');
	uartwrite('-');
	say_two_bytes(redData);
	uartwrite('G');
	uartwrite('-');
	say_two_bytes(greenData);
	uartwrite('B');
	uartwrite('-');
	say_two_bytes(blueData);
	uartwrite('W');
	uartwrite('-');
	say_two_bytes(whiteValue);
	uartwrite('S');
	uartwrite('-');
	say_two_bytes(sum);
	return determine_color(redData, greenData, blueData);
}

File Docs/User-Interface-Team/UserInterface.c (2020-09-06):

#include <stdbool.h>
#include <stdint.h>

//This code sets up a basic state machine. Using an interrupt, two buttons and a RGB LED, the user can control the color of the LED.
//Interrupt handler is at the end of the startup file. Important lines in startup file are 57 and 58 and after 365.

//Variables
int flag;//turned on when interrupt is hit. turned off once next state is defined
int current_state;//state register
int next_state;//next state

void clock_50Mhz() {
	
    unsigned long *rcc =(unsigned long*)(0x400FE000+0x60);
    unsigned long *rcc2 =(unsigned long*)(0x400FE000+0x70);
    unsigned long *ris =(unsigned long*)(0x400FE000+0x50);
    unsigned long *rcgcgpio =(unsigned long*)(0x400FE000+0x608);

    *rcc2 = *rcc2 | (1<<31);            //USERCC2
    *rcc2 = *rcc2 | (1<<11);            //BYPASS
    *rcc = *rcc &(~(1<<22));            //CLEAR USESYSDIV
    *rcc = *rcc &(~(0x1F<<6));          //CLEAR XTAL
    *rcc = *rcc | (0X15<<6);            //XTAL
    *rcc2 = *rcc2 &(~(0x7<<4));         //CLEAR OSCSRC
    *rcc2 = *rcc2 &(~(0x1<<13));        //CLEAR PWRDN
    *rcc2 = *rcc2 &(~(0x3F<<23));       //CLEAR SYSDIV2
    *rcc2 = *rcc2 | (0x3<<23);          //SYSDIV2
    *rcc = *rcc | (0x1<<22);            //USESYSDIV

    while(!(*ris&(0x1<<6)))               //POLL PLLRIS
        continue;

    *rcc2 = *rcc2 &(~(0x1<<11));        //CLEAR BYPASS

    *rcgcgpio = *rcgcgpio | (0x5<<3); //make sure to attach to the ports you are using (F and D)

}

void configure() {

    //Port D. Set up for switch inputs PD0 and PD1
    unsigned long *gpiolockD   = (unsigned long *) (0x40007000 + 0x520);
    unsigned long *gpiocrD     = (unsigned long *) (0x40007000 + 0x524);
    unsigned long *gpiopurD    = (unsigned long *) (0x40007000 + 0x510); 
    
    unsigned long *gpiodirD    = (unsigned long*)(0x40007000 + 0x400);    
    unsigned long *gpioafselD  = (unsigned long*)(0x40007000 + 0x420);  
    unsigned long *gpiodenD    = (unsigned long*)(0x40007000 + 0x51c);    
    
    //Port F. Set up for LEDs, PF1, PF2, PF3. Set up interrupt, PF0, PF4 (redundant here)
    unsigned long *gpiolock   = (unsigned long *) (0x40025000 + 0x520);
    unsigned long *gpiocr     = (unsigned long *) (0x40025000 + 0x524);
    unsigned long *gpiopur    = (unsigned long *) (0x40025000 + 0x510); //pull up resistor
    
    unsigned long *gpiodir    = (unsigned long *) (0x40025000+0x400);    //adress for all F direction
    unsigned long *gpioafsel  = (unsigned long *) (0x40025000+0x420);  //adress for all F alternate functions
    unsigned long *gpioden    = (unsigned long *) (0x40025000+0x51c);    //adress for all F enable
    
    unsigned long *gpiois     = (unsigned long *) (0x40025000 + 0x404); //edge/level sensitivity
    unsigned long *gpioibe    = (unsigned long *) (0x40025000 + 0x408); //set to 0 to be sensitive to one edge
    unsigned long *gpioiev    = (unsigned long *) (0x40025000 + 0x40c); //selects rising or falling edge
    unsigned long *gpioris    = (unsigned long *) (0x40025000 + 0x414);
    unsigned long *gpioim     = (unsigned long *) (0x40025000 + 0x410); //interrupt control bit 6
    unsigned long *nvicpri7   = (unsigned long *) (0xE000E000 + 0x41c); //interrupt priority
    unsigned long *nvicen0    = (unsigned long *) (0xE000E000 + 0x100); //enable interrupt

    //switch setup Port F
    
    *gpiolock   = 0x4C4F434B;
    *gpiocr     = 0x11;
    *gpiopur    = 0x11;

    //Port F setup

    *gpioafsel  = 0x00;
    *gpiodir    = 0xE; //sets up the output PF1, PF2, PF3
    *gpiodir    = (*gpiodir & ~(0x11)); //sets up input PF0 and PF4                                                                                                   //turns alternate functions off
    *gpioden    = 0xFF;

    //switch setup Port D for pins 0 and 1 as switch inputs
    
    *gpiolockD   = 0x4C4F434B; //unlocks switch
    *gpiocrD     = 0x3;
    *gpiopurD    = 0x3; //pull up resistor

    //Port D setup for pins 0 and 1 as switch inputs

    *gpioafselD  = 0x00;
    *gpiodirD    = (*gpiodirD & ~(0x3)); //switch inputs PD0 and PD1                                                                                                   //turns alternate functions off
    *gpiodenD    = 0xFF;                                                                       

    //interrupt controls

    *gpioim     = 0x00;
    *gpiois     &= ~(0x11); //sets to edge sensitivity
    
    *gpioibe    = 0x00; //sesnitive to one edge
    *gpioiev    |= 0xFF; //sets which edge
    *gpioris    = 0x00;

    *nvicpri7   = (1 << 21); //priority 7
    *nvicen0    = (1 << 30); //interrupt #30 enable
    *gpioim     = 0x11;

    //initialize variables
    
    flag                = 0;
    current_state       = 0;
    next_state          = 0;

}

// Defining the states. Each state, for the time being, only outputs a solid color. Can create more states here

//yellow LED shown (green and blue at the same time) PF2 and PF3. when current_state = 0
void standby(){

    unsigned long *gpiodata = (unsigned long*)(0x40025000+0x000+(0x1F<<2));

    //output of state
    while(flag==0){
        
        *gpiodata = 0xB; //color defined here  
    
    }
}
//Green LED shown PF3. when current_state = 1
void green_state(){

    unsigned long *gpiodata = (unsigned long*)(0x40025000+0x000+(0x1F<<2)); 
    
    //output of state
    while(flag==0){
        
        *gpiodata = 0x08; //color defined here 
    
    }
}
// LED Blue PF2. when current_state = 2
void blink_state(){

    unsigned long *gpiodata = (unsigned long*)(0x40025000+0x000+(0x1F<<2)); 
    
    //output of sate
    while(flag==0){
        
        *gpiodata = 0x04; //color defined here 
    }
}
//Other State. Red LED. when current_state = 3
void other_state(){

    unsigned long *gpiodata = (unsigned long*)(0x40025000+0x000+(0x1F<<2)); 
    
    //output of sate
    while(flag==0){

        *gpiodata = 0x02; //color defined here  

    }
}

//used to kind of debounce in handler
void delay (unsigned long d){                       

    for(int i=0; i < d; i++){}

}

//based on current_state, decides which state to execute. Can add as many states as desired
void Decide_Current(){

    if(current_state == 0){
        
        standby();
    }

    else if(current_state == 1){
        
        green_state();
    
    }

    else if(current_state == 2){

        blink_state();

    }

    else if(current_state == 3){

        other_state();

    }

}
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

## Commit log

2020-06-30 Uploaded universal motor controller files
2020-06-30 Added universal motor controller design document
2020-07-01 Added Stepper Development document
2020-07-26 Split main file into stepper, init, and umc
2020-08-01 Fixed incorrect direction definitions
    [stepper.c, umc.c]
2020-08-01 Added sorter.c for testing motor functions in software
2020-08-01 Reorganized stepper documents and sorter files
2020-08-01 Integrated sensor to motor control
2020-08-06 Reorganized files, removed dependency on _init file for stepper.c
2020-08-06 Separated I2C.c into smaller modules
2020-08-07 Modified sorter.c for updated sensor code
2020-08-07 Fixed bugs with split file integration
    [color_process.c, color_sensor.c, sorter.c]
2020-08-08 Added pwm to sorter.c
2020-08-08 Fixed motor control
2020-08-09 Modified stepper functions to take pin number as argument for switches
2020-08-09 Fixed limit switch addressing
    [stepper.c]
2020-08-09 Switched to SW1 for test home switch
2020-08-12 Added call diagrams for stepper functions
2020-08-17 Added interrupt register addresses
2020-08-20 Added reference for designing PCBs in KiCad
2020-08-24 Added progress reports and PCB design documents
    -Added Progress reports for missing 6 weeks of development
    -Added stepper driver PCB design specifications
    -Added stepper driver PCB development progress
2020-09-13 Fixed outdated stepper.c comment
    [stepper.c]
2020-09-13 Configured interrupt registers, implemented start/stop isr
2020-11-08 Fixed start button interrupt call
    [startup.c]
2020-11-08 Marked start and stop switches in sorter.c
2020-11-22 Add files via upload
    Added all current Image Processing files including all pictures used.
